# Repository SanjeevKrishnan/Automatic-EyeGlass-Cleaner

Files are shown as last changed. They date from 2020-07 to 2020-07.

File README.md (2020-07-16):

# Automatic EyeGlass Cleaner
Inter IIT Tech Meet 2019

## Abstract

Aim of this project is to make a self-automated Eyeglass Cleaner that can cleanse and dry any spectacles.

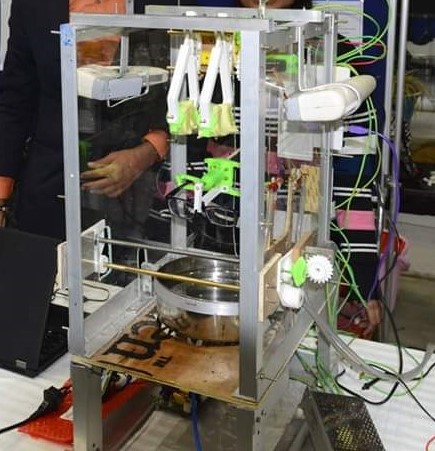
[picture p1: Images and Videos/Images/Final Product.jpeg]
Final Product


## Motivation

<p align="justify">In this fast and busy world, we fail to take care of our own minute personal cleanliness. But when we enter the professional world, all these small things get noticed. And also, these small things pile up to big issues which in turn affects us directly. In this, our spectacles take a major part because eyes are our index. An easily operable machine which can clean our spectacles during our coffee time will be of high use, especially in professional and public spaces.<br><br>Eyeglasses cleaners available presently in the market are costly but are not versatile. They either do ultrasonic cleaning or splashing water and drying. But still, it leaves smudges on the lenses. And also they might take much time for this simple task and majorly nowhere automatic wiping is available. This process is clumsy and can be automated which would give the user complete hands-free experience.<br><br>So we planned on designing a machine that can clean, rinse, dry, and wipe the eye-glass in less time.</p>

## Components

* 2x Air Blower
* Capacitors
* 2x Cytron Motor Drive
* 1x DC 900 rpm motor
* 2x DC 300 rpm motor
* 2x DC Solenoid Valve
* Fuse
* Inductors
* 1x 12V DC Power Adapter
* Relay
* 4x 5V Relay Module
* Resistors
* 1x Rotary Encoder
* 1x Servo Motor
* Transformers
* Transistors
* Ultrasonic Transducer
* 1x Water Pump

## Workflow

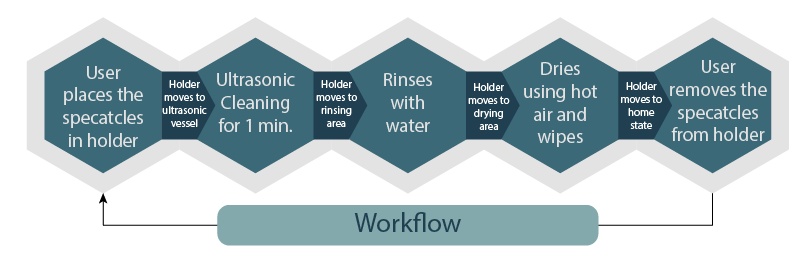
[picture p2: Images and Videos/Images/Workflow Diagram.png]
Worflow Diagram


## Mechanical Aspect of the Design

### Structure

<p align="justify">It is a cuboidal frame structure made up of aluminum channel covered with transparent acrylic sheets to allow users to see the whole cleaning process. Wiper and hot air blower are placed at the top, water rinser is placed at the middle, and ultrasonic cleaning vessel is placed at the bottom. Water storage is placed above the structure, ultrasonic circuit, and water pump is placed in a separate chamber below ultrasonic vessel separated by plywood and all other electronic components are placed at the backside of the structure separated from the structure by acrylic sheet to protect components from water.</p>

### Holder

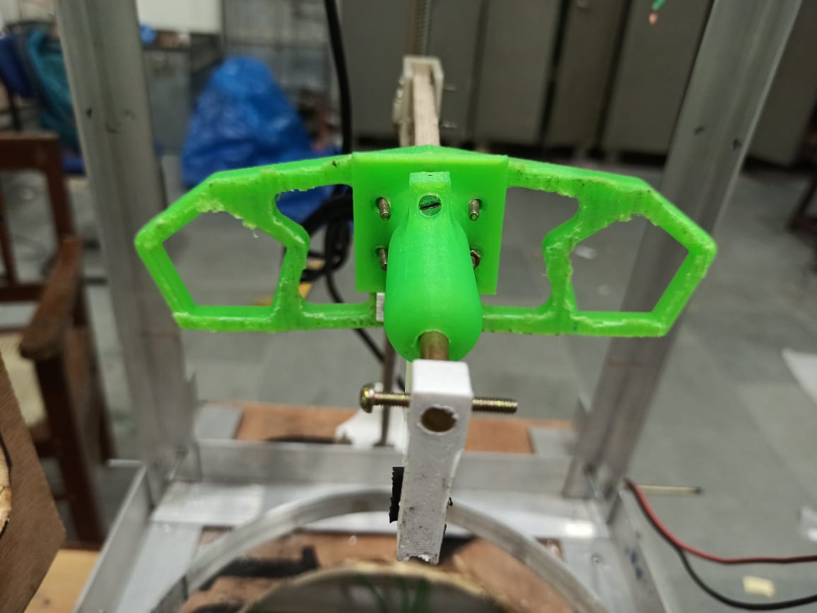
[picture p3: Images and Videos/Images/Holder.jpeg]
Holder


We have designed a special holder for mounting the eyeglasses. Eyeglasses comes in different shapes and sizes. So we have made a holder that can adjust itself to hold all types of eyeglasses.

### Ultrasonic Cleaning

<p align="justify">There is a vessel at the bottom which is connected with an ultrasonic transducer which produces ultrasonic waves in the liquid filled inside the vessel by changing electrical signals to mechanical waves. The waves create cavitation in the liquid. These cavitations collapse with enormous energy due to which high temperature and pressure are generated and thus help in cleaning the glasses.</p>

### Rinsing

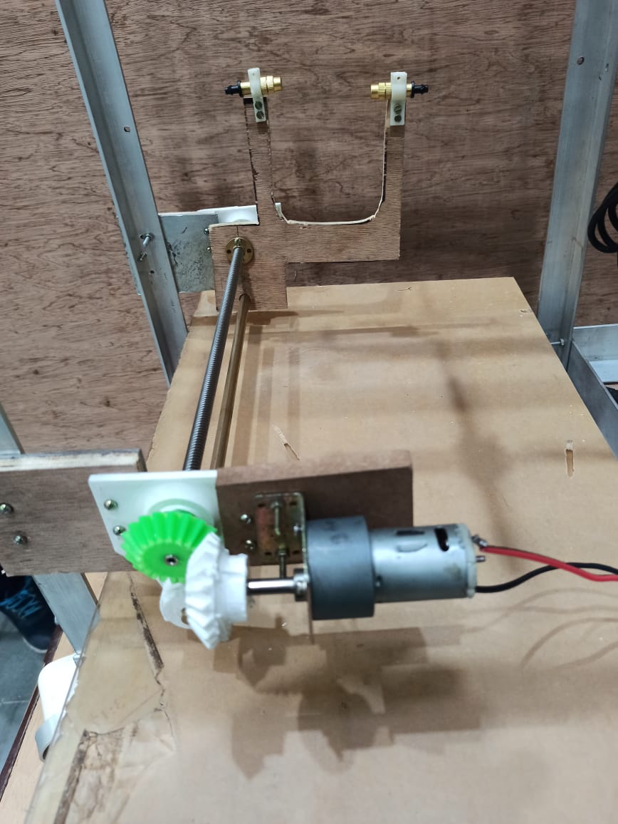
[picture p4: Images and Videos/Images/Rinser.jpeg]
Rinser


<p align="justify">After ultrasonic cleaning, eye-glass is lifted to the middle of the machine where it is rinsed with water with the help of a ‘U’ shaped structure with two nozzles placed in front and back of the lenses. This rinser runs perpendicular to the eyeglass splashing water on the eyeglasses.</p> 

### Drying and Wiping

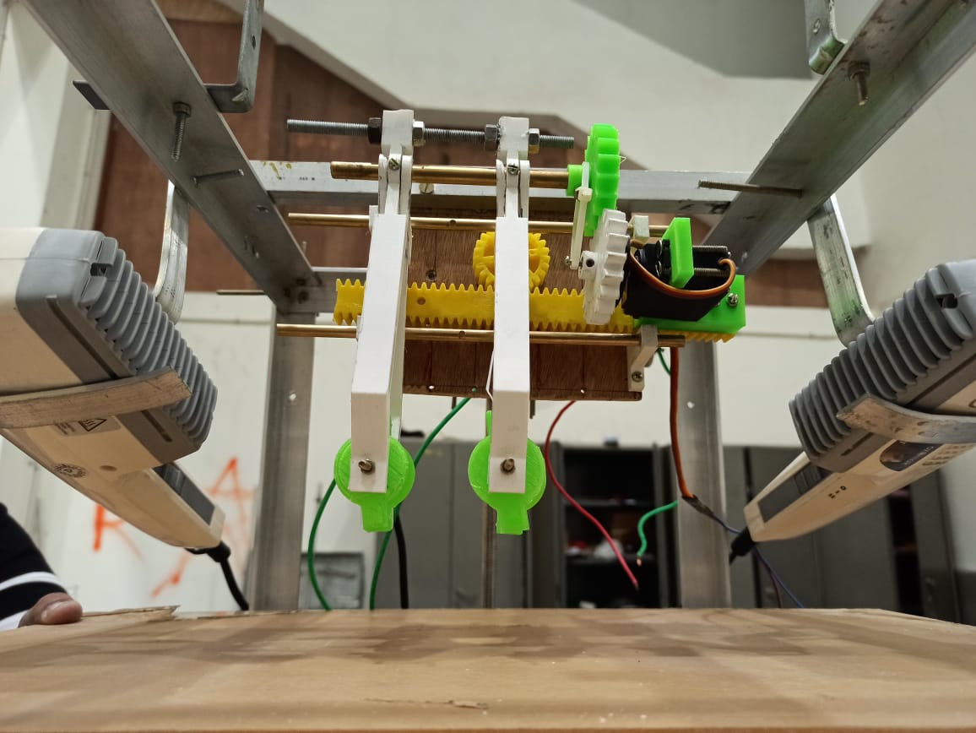
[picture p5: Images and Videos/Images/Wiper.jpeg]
Wiper


<p align="justify">After rinsing, eyeglasses move to the last level, to the top of the machine, where it is dried and wiped. There are hot air blowers on the two side walls of the machine which blows hot air on the spectacle which helps in removing wetness from the frame. Then it is wiped with a sponge wrapped with a microfiber cloth. There are 4 circular disks with this kind of wiping material covering both sides of both the lenses. This wiper works on the rack and pinion mechanism.</p>

### Traversal

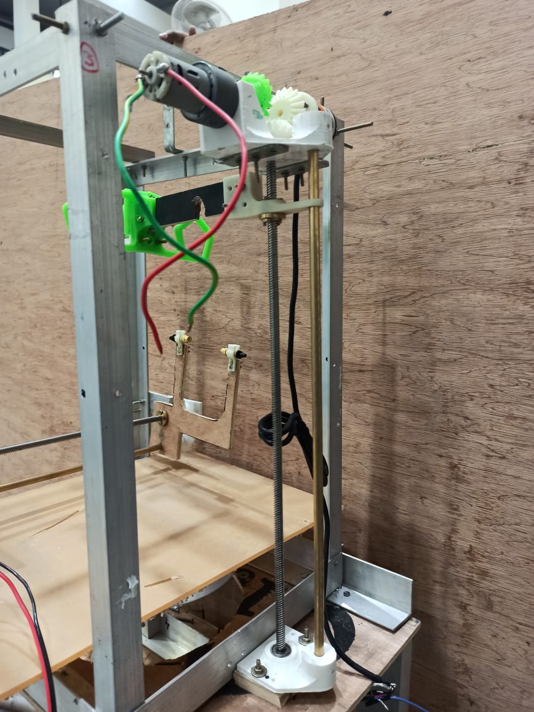
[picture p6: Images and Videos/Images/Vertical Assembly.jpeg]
Vertical Assembly


<p align="justify">The eyeglass holder is connected to a vertical lead screw which helps the eye-glass to move to different levels for different processes. This vertical lead screw is operated by a 900 rpm DC motor which is placed perpendicular to the lead screw and both are coupled with a pair of bevel gear. Its feedback is taken with the help of a rotary encoder which is again placed in the same fashion as the motor.</p>

## Electronics Aspect of the Design

### Microcontroller

Arduino Mega 2560 R3 is used as the microcontroller board.

### Sensors

* Rotary Encoder is used to get the coordinate feedback of vertical assembly(holder).
* Hall Sensor is used to sense the home state(start position) of vertical assembly.

### Actuators

* Johnson 900 rpm DC motor is used for traversal of the holder.
* Johnson 300 rpm DC motors are used for traversal of the rinser and movement of wiper.
* Servo Motor is used for wiping action.

### Other Controllers

* Cytron Motor driver is used to control DC motors
* 5V Relay module is used to switch on/off the ultrasonic cleaner, water pump, and air blowers.

### Other Components

* DC 12V 80W water pump is used to spray water during rinsing action.
* 12V Solenoid Valves are used to control water movement between the tank and ultrasonic vessel

### Power

* Ultrasonic Cleaner circuit and air blowers are directly powered from 220V AC supply.
* 12V DC Power Adapter is used to convert 220V AC to 12V DC to power solenoid valves, water pump, and motor drivers.
* IC LM7809, IC LM7806, IC LM7805 are used to convert 12v DC to 9V DC, 6V DC, 5V DC respectively to power Arduino, servo motor, encoder, relay module.

## Cost Structure

| **Components** |**Cost(INR.)**|
|---|---|
| Air Blower | 1300 |
| Aluminium Channels and Rods | 800 |
| Arduino Mega | 800 |
| Capacitors | 300 |
| Cytron Motor Driver | 3000 |
| DC Motors | 1050 |
| DC Solenoid Valve | 250 |
| Fuse | 35 |
| Hose, Pipes, and Brass connectors | 450 |
| Inductors | 150 |
| Power Adapter | 1500 |
| Relay | 100 |
| Relay Module | 450 |
| Resistors | 900 |
| Rotary Encoder | 1500 |
| Servo Motor | 150 |
| Transformer | 230 |
| Transistors | 100 |
| Ultrasonic Transducer | 800 |
| Water Pump | 700 |
| Miscellaneous | 235 |
| **Total** | **14000**  |

## Applications

* Optical showrooms-To clean customers’ spectacles
* Eye clinics - To clean patients’ spectacles
* Theatres - To clean 3D glasses 
* Offices - Workers can clean their spectacles
* Shopping Malls - People can spend their wait time in cleaning their spectacles

## Limitations

* Time taken per eyeglass is bit high.
* Ultrasonic cleaning circuit has to be switched on manually.

## Future Improvements

* Actuations can be made fast to reduce cleaning duration.
* Indications and Error messages can be displayed using an LCD display module.
* Ultrasonic Cleaning process can also be automated.

## Team Members

1. [Panuganti Shiva Sri Teja Kumar](https://github.com/shivasriteja)
2. [Rishika Chandra](https://github.com/chandrarishika14)
3. [Sanjeev Krishnan R.](https://github.com/SanjeevKrishnan)
4. [Suja G.](https://github.com/suja-g)
5. [Ujjwal Baranwal](https://github.com/ujjwal-baranwal)
6. [Yashutosh Bansal](https://github.com/yashutoshbansal)
7. [Yawan Gupta](https://github.com/yawangupta)

## Mentors

1. [Anant Shandilya](https://github.com/Anant-Shandilya)
2. [Shubhanshu Agarwal](https://github.com/Shubhanshu07)

## References

<https://techblog.ctgclean.com/2012/01/ultrasonics-transducers-resonance/>

<https://www.americanpiezo.com/standard-products/ultrasonic-power-transducers.html>

<https://www.allaboutvision.com/en-in/eyeglasses/faq/eyeglass-frame-size/>

<https://www.svce.ac.in/departments/physics/ph16151/UNIT%204%20Ultrasonics%20.new.pdf>

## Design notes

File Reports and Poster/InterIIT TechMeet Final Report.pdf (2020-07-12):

# Engineer’s Conclave

Low-Prep Event (150 Points)

# Project Report

## Project Name: Automatic Eyeglass Cleaner

## Institute Name: Indian Institute of Technology Roorkee

## Team:

Serial No. | Team Member Name | Enrollment No.
1. Panuganti Shiva Sri Teja | Kumar | 18113091
2. | Rishika Chandra | 18115084
3. | Sanjeev Krishnan R. | 18110021
4. | Suja G. | 18122025
5. | Yawan Gupta | 17118080

## Problem addressed:

Eyeglasses cleaners available presently in the market are costly but are not versatile. They either do ultrasonic cleaning or splashing water and drying. But still, it leaves smudges on the lenses. And also they might take much time for this simple task and majorly nowhere automatic wiping is available. This process is clumsy and can be automated which would give the user complete hands-free experience.

So we planned on designing a machine that can clean, rinse, dry and wipe the eye-glass in less time.

## Proposed Solution:

We have designed and manufactured a machine which cleans the eyeglasses automatically by combining four processes-
1. Ultrasonic cleaning
2. Rinsing
3. Drying
4. Wiping

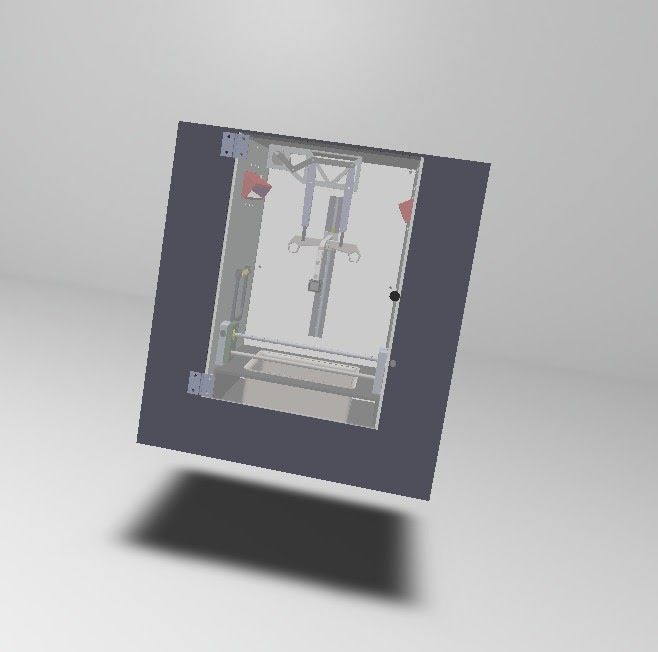
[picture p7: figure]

It cleans the eyeglass with ultrasonic waves which helps it to clean the nook and corner. Then it is rinsed with water by splashing water jet on lenses which helps in removing smudges and fingerprints. Then it is dried by blowing mild hot air to remove wetness on the frame and then wiped with specially designed wiping material wrapped with a microfiber cloth which gives crystal clear appearance to the glasses.

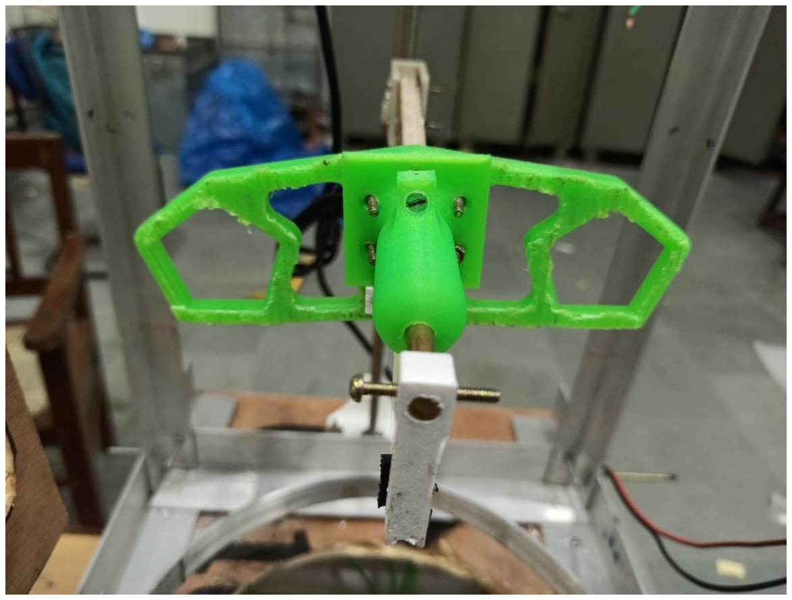
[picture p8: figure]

Mounting the Eye-Glasses

We have designed a special holder for mounting the eyeglasses. Eyeglasses comes in different shapes and sizes. So we have made a holder that can adjust itself to hold all types of eyeglasses.

Movement of Eyeglasses to different levels

The eyeglass holder is connected to a vertical lead screw which helps the eye-glass to move to different levels for different processes. This vertical lead screw is operated by a 900 rpm DC motor which is placed perpendicular to the lead screw and both are coupled with a pair of bevel gear. Its feedback is taken with the help of a rotary encoder which again placed in the same fashion as the motor.

Ultrasonic Cleaning

There is a vessel at the bottom which is connected with an ultrasonic

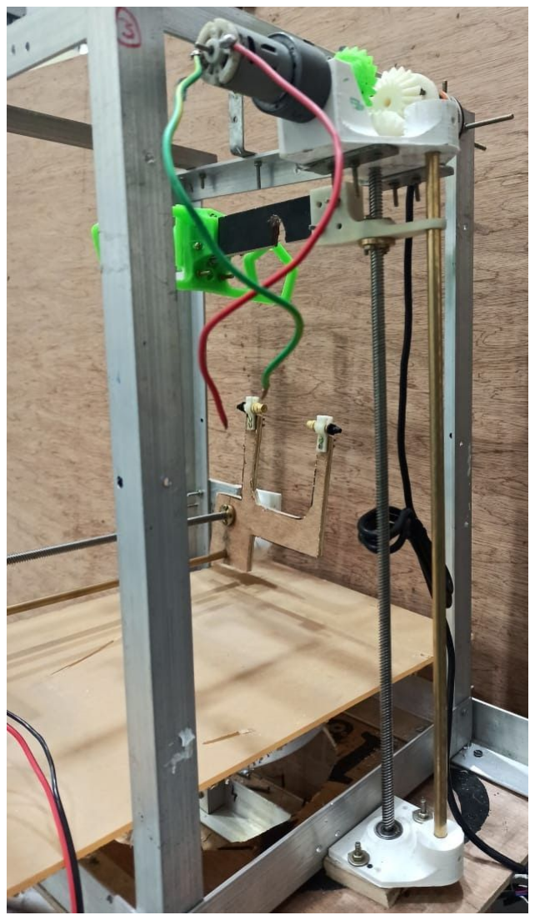
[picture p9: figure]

transducer which produces ultrasonic waves in the liquid filled inside the vessel by changing electrical signals to mechanical waves. The waves create cavitation in the liquid. These cavitations collapse with enormous energy due to which high temperature and pressure are generated and thus help in cleaning the glasses.

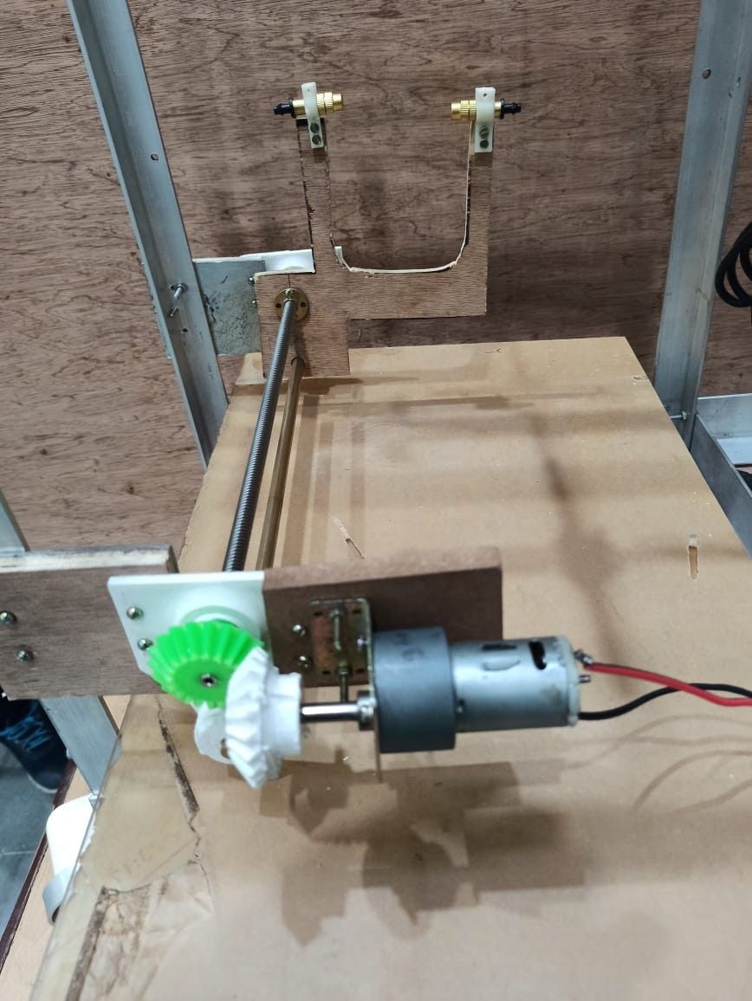
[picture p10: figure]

Rinsing

After ultrasonic cleaning, eye-glass is lifted to the middle of the machine where it is rinsed with water with the help of a ‘U’ shaped structure with two nozzles placed in front and back of the lenses. This rinser runs perpendicular to the eyeglass splashing water on the eyeglasses.

Drying and Wiping

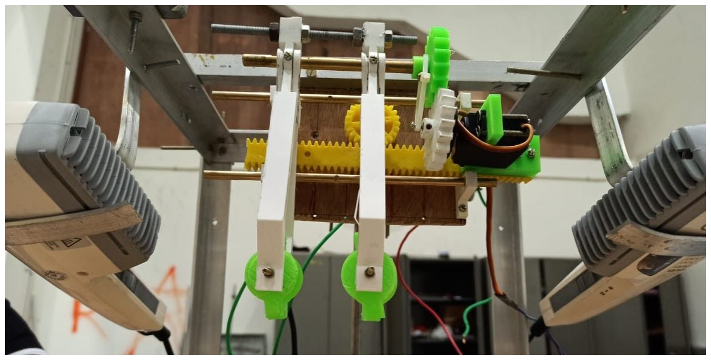
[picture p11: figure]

After rinsing, eyeglasses move to the last level, to the top of the machine, where it is dried and wiped. There are hot air blowers on the two side walls of the machine which blows hot air on the spectacle which helps in removing wetness from the frame. Then it is wiped with a sponge wrapped with a microfiber cloth. There are 4 circular disks with this
kind of wiping material covering both sides of both the
lenses. This wiper works on the rack and pinion mechanism.

After wiping is done holder is again brought back down from where it is taken out by the user.

## Summary:

## - Test Results:

We tried wiping with wiper working on a double scotch yoke mechanism in which one actuator is used to do two motions in the perpendicular direction(moving wiper parallel and the open wiper). It was not much efficient. The required force was not acquired. So we changed it to rack and pinion mechanism in which we use one actuator for sliding the wiper along spectacles and one servo motor for sweep action of the wiper.
We tried drying the spectacle with two normal hair dryers. It was taking more time than expected. So we have attached one more blower on the top.
We tried ultrasonic cleaning with one transducer to transmit ultrasonic waves. Each transducer has some range of area coverable. Expectations were not met as our area of the vessel was more than that of the allowed range of the transducer. So we added one more transducer. Now the whole surface is covered and expectations are met.

## - Surveys:

We made surveys on the sizes of lenses. The average range of temple length came out to be 120mm to 150mm. The average bridge length ranges from 14mm to 24mm and the width of lenses ranges from 40mm to 62mm.

We made a survey to find approximately how much time one person would wish to spend to clean his eye-glass. Results came out to be 1-2 mins.

## - References:

- https://techblog.ctgclean.com/2012/01/ultrasonics-transducers-resonance/
- https://www.americanpiezo.com/standard-products/ultrasonic-power-transducer s.html (https://www.americanpiezo.com/standard-products/ultrasonic-power-transducers.html)
- https://www.allaboutvision.com/en-in/eyeglasses/faq/eyeglass-frame-size/
- https://www.svce.ac.in/departments/physics/ph16151/UNIT%204%20Ultrasoni cs%20.new.pdf (https://www.svce.ac.in/departments/physics/ph16151/UNIT%204%20Ultrasonics%20.new.pdf)

## - Video Links

*
:

(* = Optional)

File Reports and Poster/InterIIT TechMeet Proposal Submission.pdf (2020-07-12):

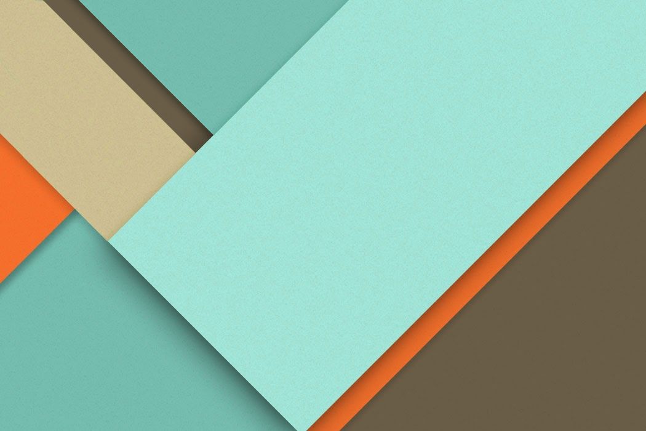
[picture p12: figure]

# Automatic Eye-Glass Cleaner

─

## Models And Robotics Section

### Indian Institute of Technology Roorkee

# Contents

─

Overview | 2
Project Motivation | 2
Other Products available in the market and their disadvantages | 2
Ultrasonic Cleaners | 2
Microfiber Handle Brush Tool | 2
OpticWash Machine | 3
Our solution | 3
Holding and Movement | 3
Cleaning | 4
Rinsing | 4
Drying | 4
Wiping | 5
Cost Structure | 5
Market Analysis | 6
Target Market | 6

## Overview

We have designed an automatic Eye-Glass cleaner which cleans the spectacles with ultrasonic cleaning technology, rinses with water and then dries it by blowing and wiping.

## Project Motivation


In this fast and busy world, we fail to take care of our own minute personal cleanliness. But when we enter the professional world, all these small things get noticed. And also, these small things pile up to big issues which in turn affects us directly. In this, our spectacles take a major part because eyes are our index. An easily operable machine which can clean our spectacles during our coffee time will be of high use, especially in professional and public spaces.

## Other Products available in the market and their

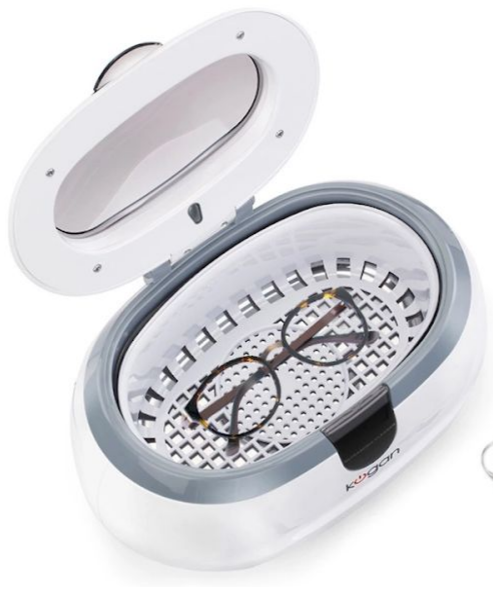
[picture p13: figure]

## disadvantages

## Ultrasonic Cleaners

- These cleaners cannot dry the glasses. So the glasses come out of the machine in a wet state and the person has to wipe it on his own.
- They can’t remove smudges from the glasses.
- These cleaners cannot rinse and wipe the glasses.

## Microfiber Handle Brush Tool

- This tool just cleans the lens. It does not help us with cleaning the frame especially corners.
- It has to be changed once in a while to get the same level of cleanliness.

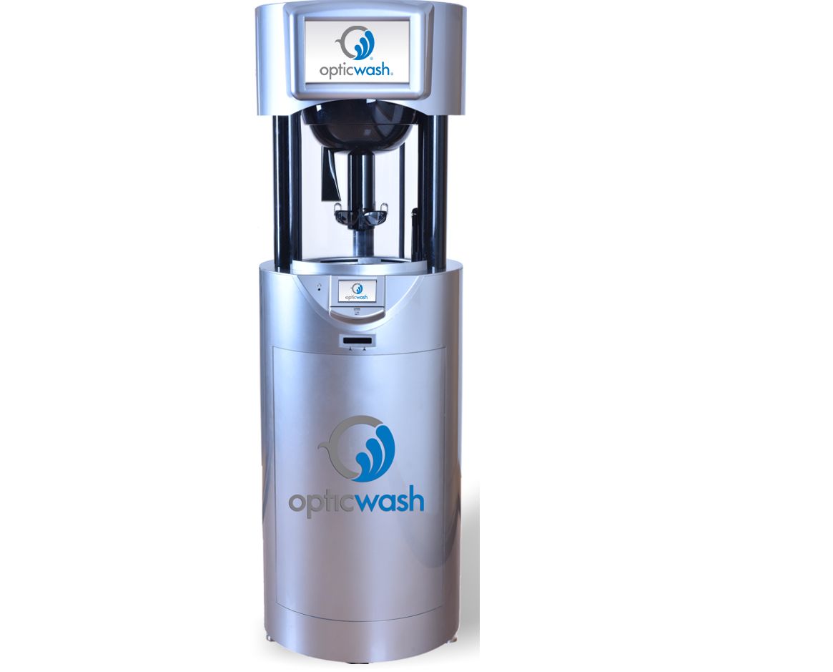
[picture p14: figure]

## OpticWash Machine

- It does not clean nook and corners as it just splashes water on the spectacles.
- Smudges do not get removed very efficiently as it is not wiping the lenses.
So, we have designed a machine which cleans with ultrasonic, rinses with water, dries by blowing air and wipes the glasses with foam so that user can use it directly out from the machine.

## Our solution

## I. Holding and Movement

In our solution, we have designed a unique spectacle holder which is easy for users to place their spectacle and also it is designed to be adjustable so that all kinds of spectacles can be placed in the holder with hassle free operation. This holder holds the spectacle at three points namely middle of bridge and starting edges of left and right temples. This holder is attached to a lead screw for easy and accurate actuation in vertical direction.

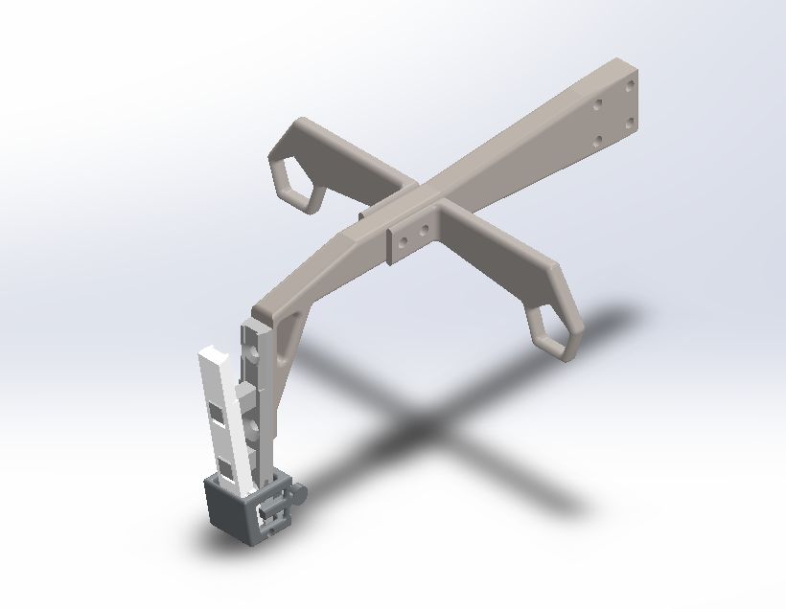
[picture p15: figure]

## II. Cleaning

In an ultrasonic cleaner, the object to be cleaned is placed in a chamber containing a suitable solution. An ultrasound generating transducer built into the chamber produces ultrasonic waves in the fluid by changing size in concert with an electrical signal oscillating at ultrasonic frequency. This creates compression waves in the liquid of the tank which creates cavitation in the liquid. These cavitation collapse with enormous energy, temperatures and pressures in the order of 5,000 K and 135 MPa is achieved. The circuit works if we drive the transducer from a square wave fed through a series LC circuit tuned to the transducer frequency. A piezoelectric ultrasonic transducer’s equivalent circuit is a capacitor in parallel with a series tuned LCR circuit. With just half an H bridge square wave drive, the transistors must charge and discharge that parallel equivalent capacitor on each half-cycle.

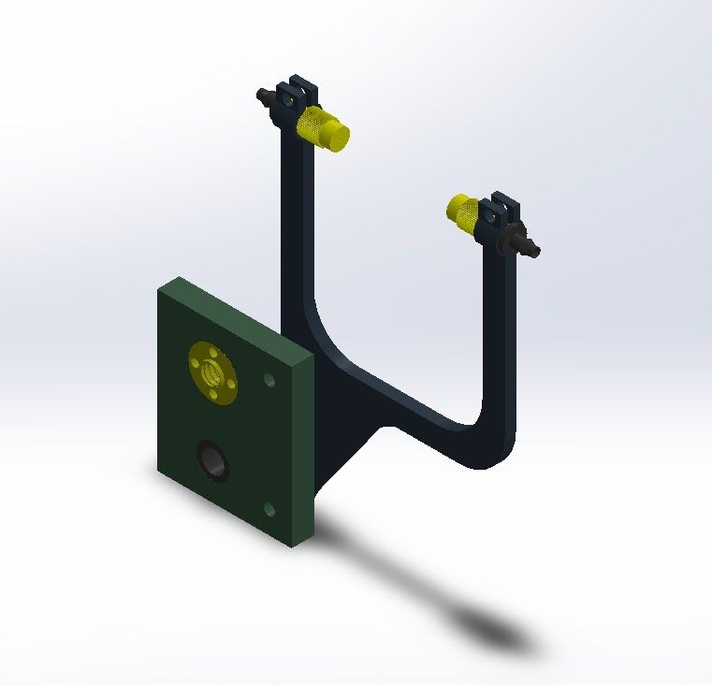
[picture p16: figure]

## III. Rinsing

After cleaning, the glasses have some chemicals solutions which need to be cleaned so we do this process by using a pump which is present in the water container. It pumps the water from container to hoes through pipes.

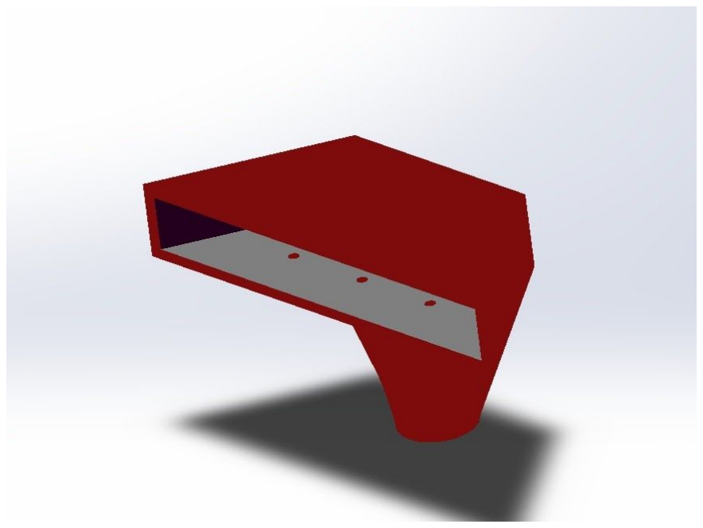
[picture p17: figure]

## IV. Drying

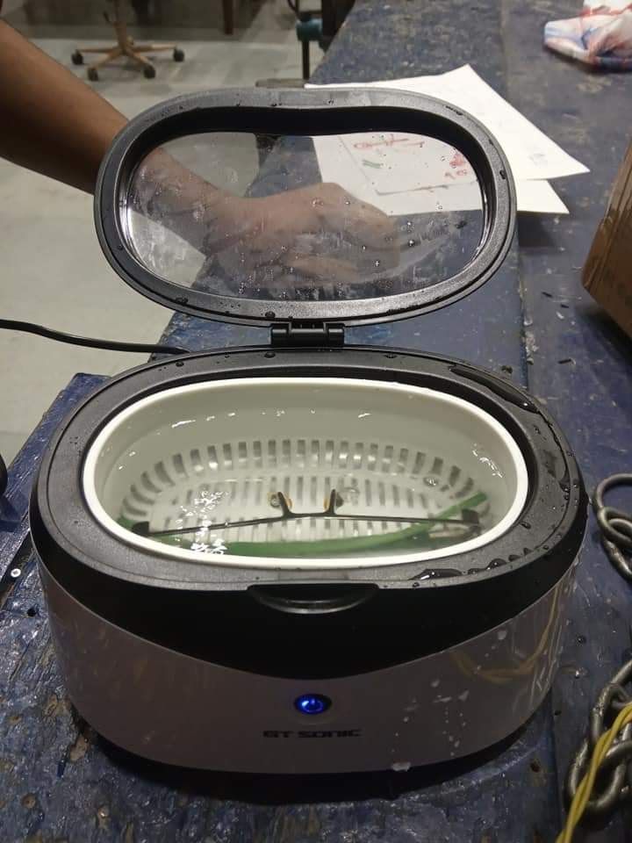
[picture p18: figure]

After rinsing, the next process is drying in which water from the glasses are removed by blowing air. In our machine, this process is carried out by the compressor which blows air through a pipe which is connected to the blower.

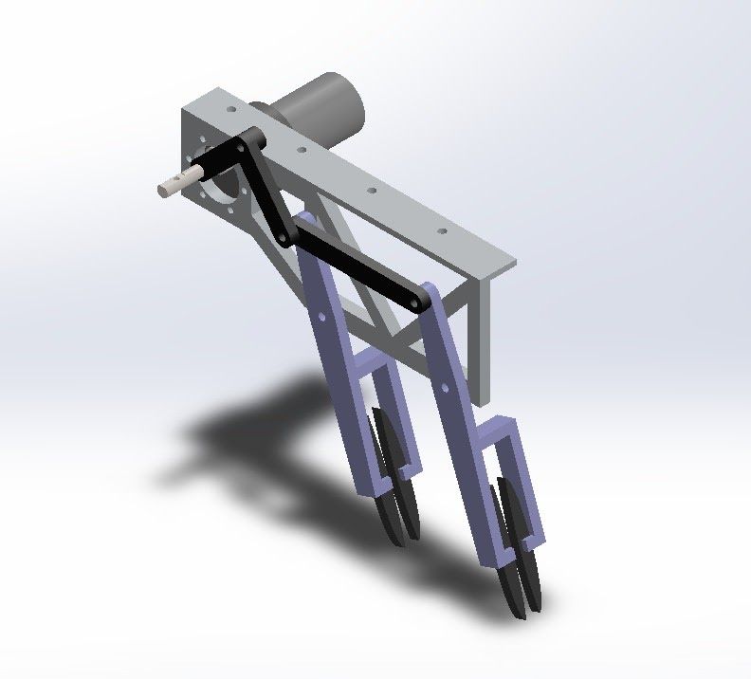
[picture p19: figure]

## V. Wiping

To remove smudges from the glasses, gentle wiping is applied by using foam which circulates on the glasses so that we get a crystal clean finish.

## Cost Structure

Components | Cost
Transformer | Rs. 230
Relay | Rs. 100
Resistors | Rs. 900
Capacitors | Rs. 300
Inductors | Rs. 150
Fuse | Rs. 35
Ultrasonic Transducer | Rs. 800
Transistors | Rs. 100
Servo motors | Rs. 150
DC Motors | Rs. 1050
Cytron Motor Drive | Rs. 3000
Rotary Encoder | Rs. 1500
Water Pump | Rs. 700
DC Solenoid Valve | Rs. 250
Relay Module | Rs.450
Power Adapter | Rs. 1500
Air Blower | Rs. 1300
Aluminium Channels and Rods | Rs. 800
Hose,Pipes and brass connecters | Rs.450
Miscellaneous | Rs. 235
TOTAL | Rs. 14000

## Market Analysis

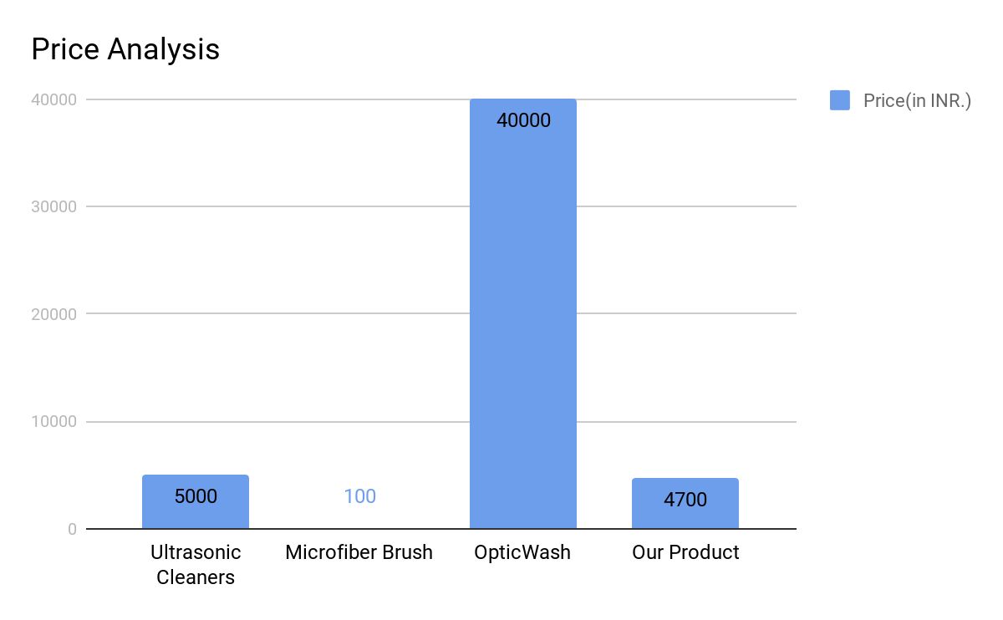
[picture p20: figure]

Ultrasonic cleaner currently available in market can only clean the eyeglass with ultrasonic mechanism which does not involve rinsing with water or drying it. OpticWash machine splashes water on eye glass and dries by blowing air but does not wipe which leave smudges on the lens. Microfiber brush can be used to wipe the lens to remove dust and smudges manually. But our product does all these things- cleaning with ultrasonic cleaner rinsing with water and drying by blowing air and also wiping it with wiper. But still we are able to produce it for around Rs. 5000. This would help our product to take a steady place in the market. Also, Rs.5000 is affordable for most of the corporate offices which is our primary target market.

## Target Market

Our spectacle cleaner can be used at-
- Optical showrooms
- Eye clinics
- Offices
- Shopping Malls
- Theatres

Optical showrooms and eye clinics is obviously a “for-sure” target market because eye-glass cleaning is one of their major jobs but they do it manually. So now we have come up with a really cheap machine which would make their job easier, more professional and of course anything done with machine gives user satisfaction. In offices where they expect you to be neat and tidy to get a professional touch, these machines would be of great use as you can get your eye glasses cleaned very fast maybe during a cup of coffee. It can be coupled with Shoe polishing machine which is already there in the market which would make a nice pair in corporate offices. Not only in the professional world, casual places like shopping mall can also be targeted. Especially in theatres user’s own eye glass can also be cleaned as it gives a good movie experience and also 3d glasses which they use in theatres can also be cleaned. As we can see we have a clear and versatile market scope in which we would get a stable place as our cost is really affordable.

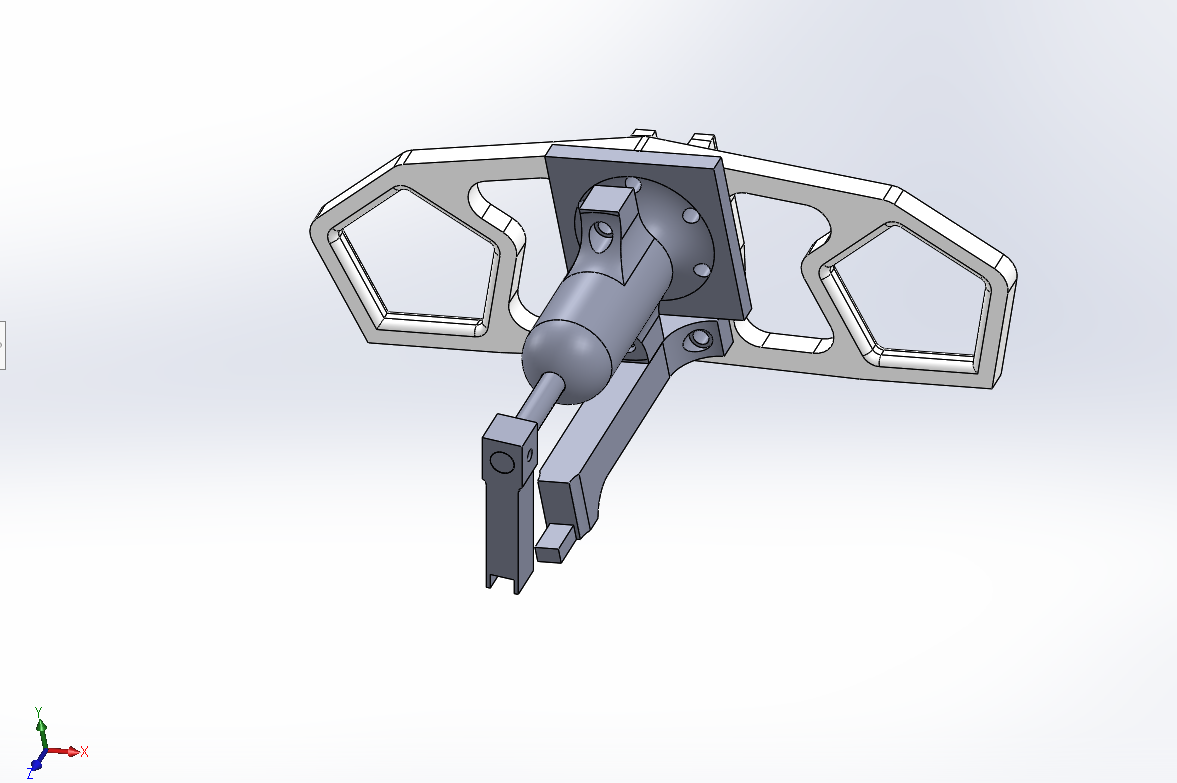
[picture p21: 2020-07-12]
Mechanical Design/Holder/Holder Design.png

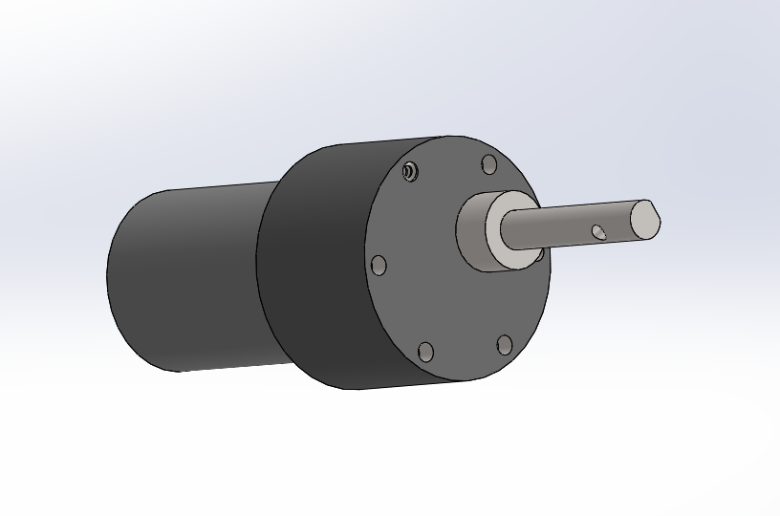
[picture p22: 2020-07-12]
Mechanical Design/Extras/DC motor.png

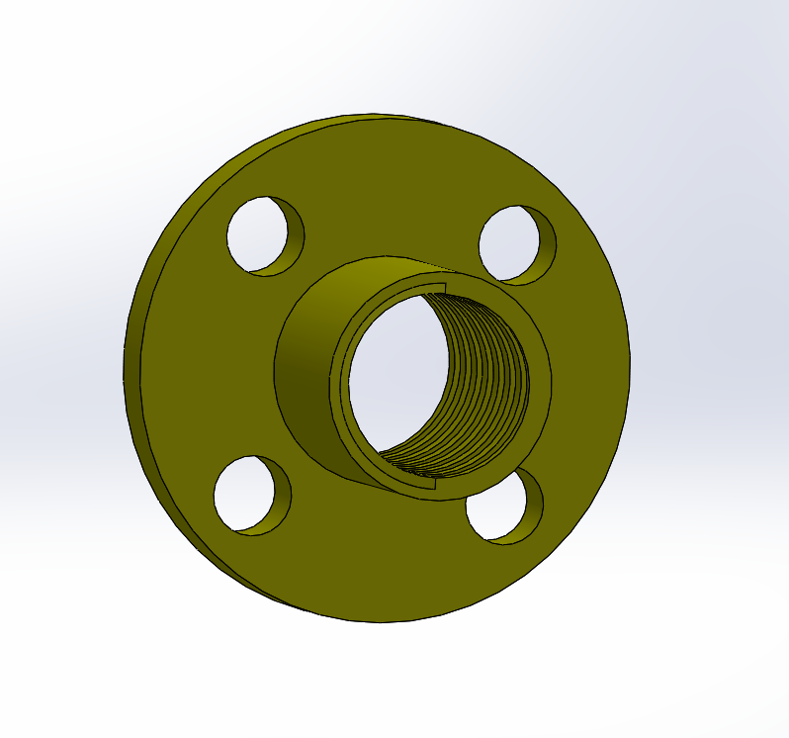
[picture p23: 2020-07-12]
Mechanical Design/Extras/8mm Slider.png

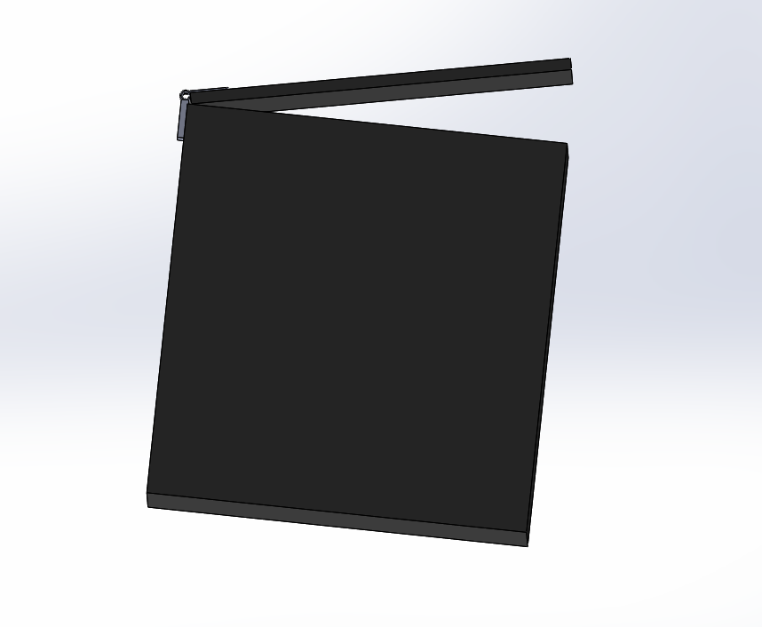
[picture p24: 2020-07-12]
Mechanical Design/Pump/Pump Box Design.png

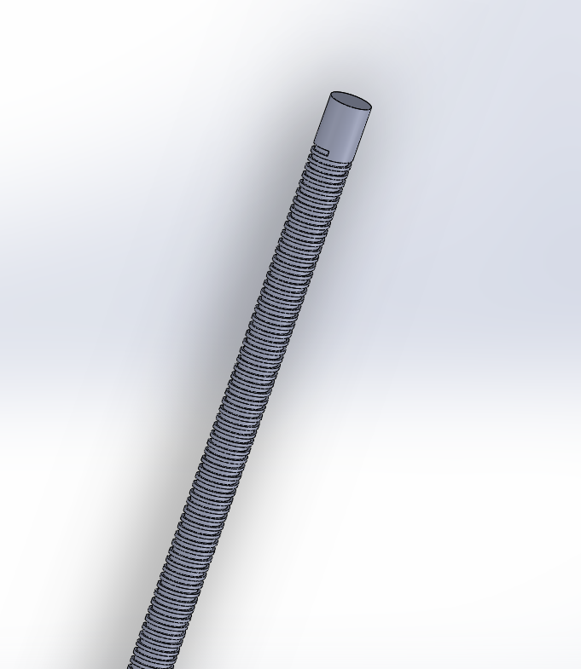
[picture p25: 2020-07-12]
Mechanical Design/Extras/Lead screw.png

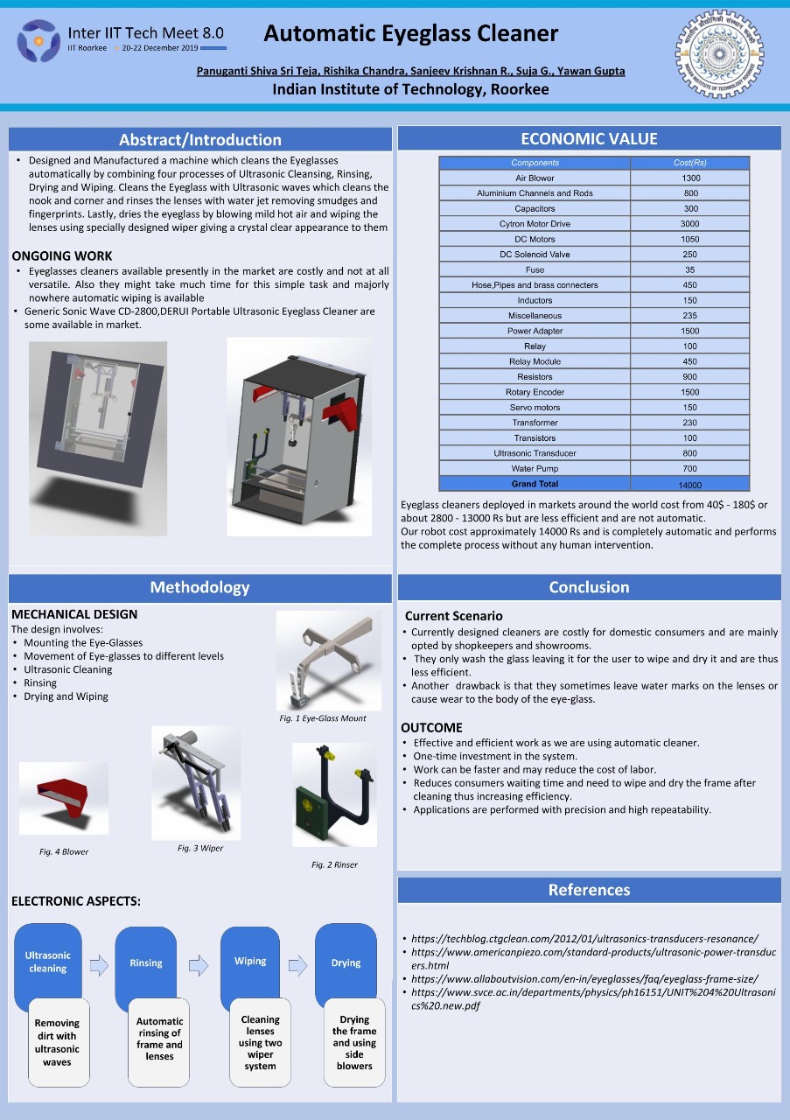
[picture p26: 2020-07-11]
Reports and Poster/InterIIT TechMeet Poster.jpeg

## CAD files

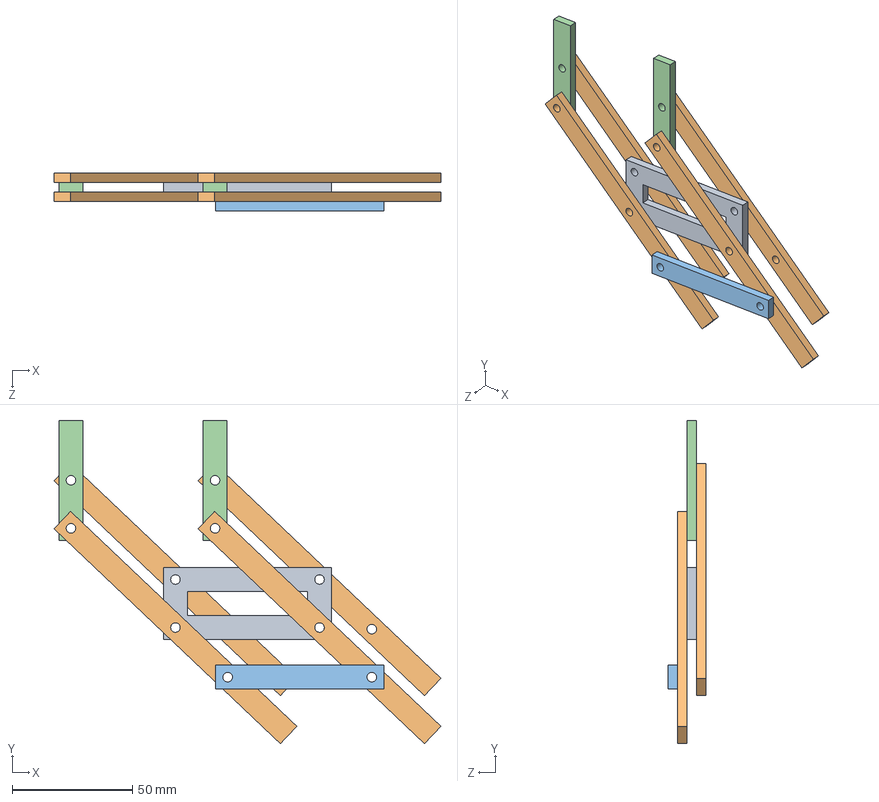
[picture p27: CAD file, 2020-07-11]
Mechanical Design/Wiper/wiper assembly.SLDASM
161.2 x 134.7 x 16.0 mm
Part1^Assem1
Part5^Assem1 x 4
Part6^Assem1
Part7^Assem1 x 2

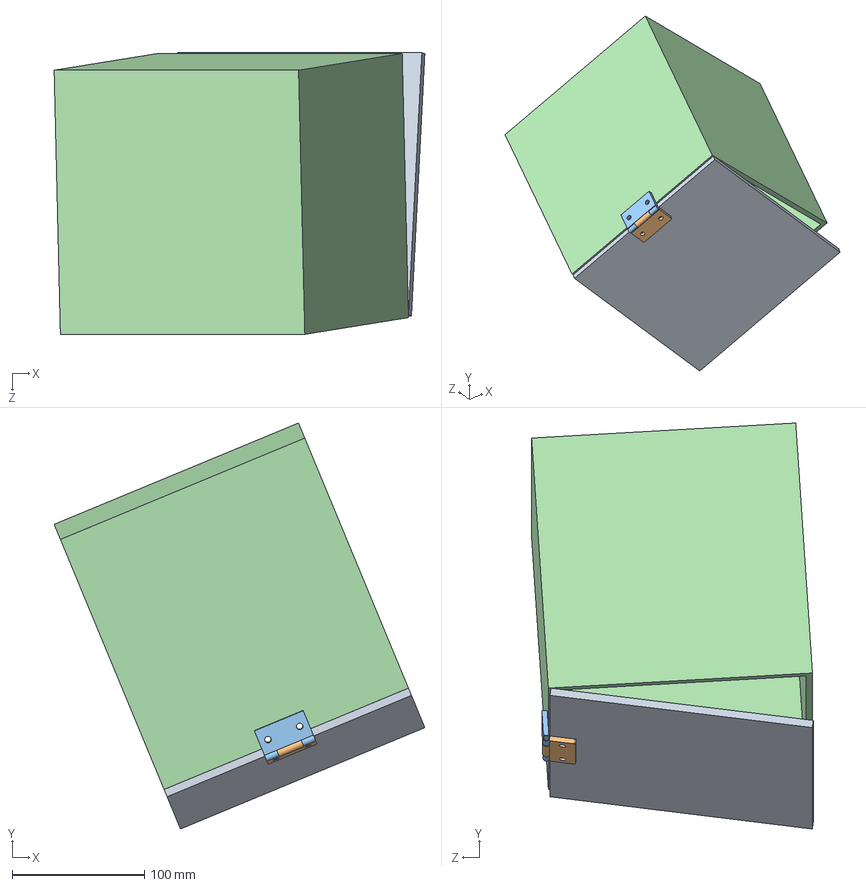
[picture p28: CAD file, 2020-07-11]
Mechanical Design/Pump/pump box.SLDASM
280.2 x 306.9 x 212.9 mm
box lid
hinge1
hinge2
pump

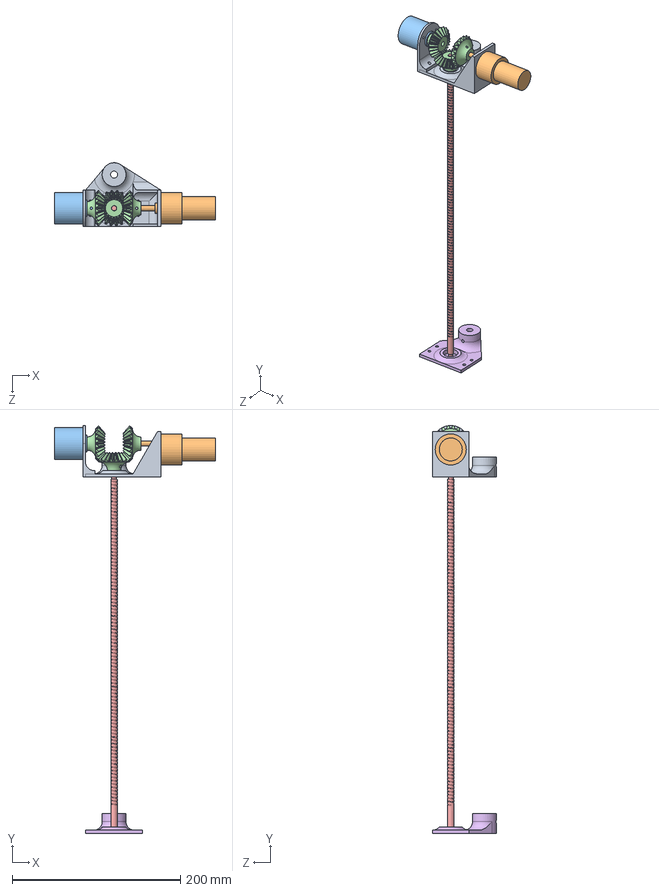
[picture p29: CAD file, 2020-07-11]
Mechanical Design/Vertical Assembly/Final VM assembly.SLDASM
191.7 x 485.5 x 75.7 mm
Motor Mount
DC motor
Encoder
Bevel gear x 3
lead screw VM
lead screw bearing block

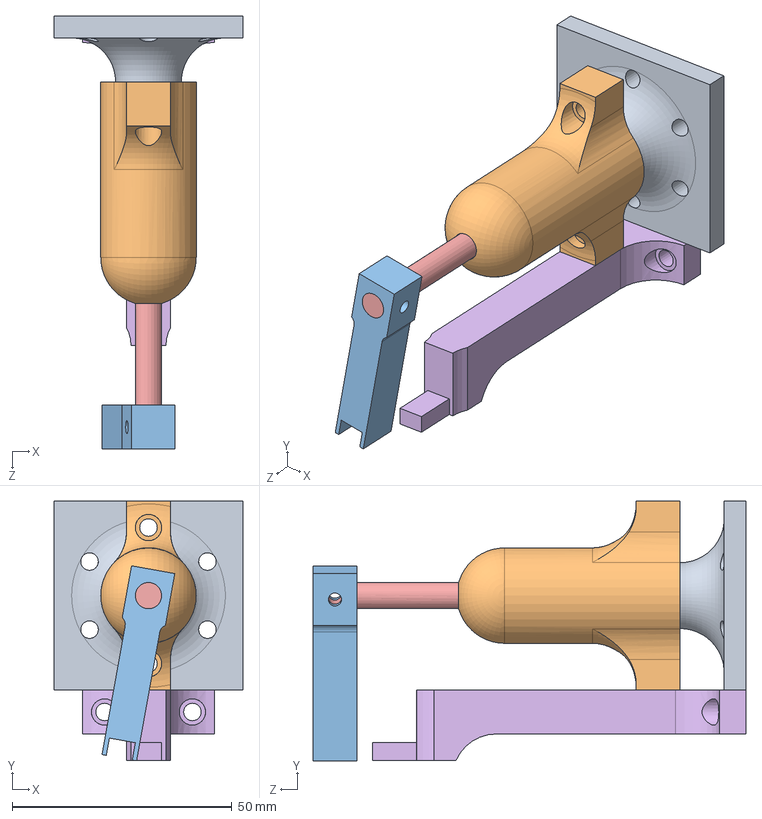
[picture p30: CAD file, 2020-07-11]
Mechanical Design/Holder/Holder assembly.SLDASM
43.0 x 59.1 x 98.6 mm
Base Lock
Lock Cover
Moving Arm
Sliding key
Rod
Base Arm

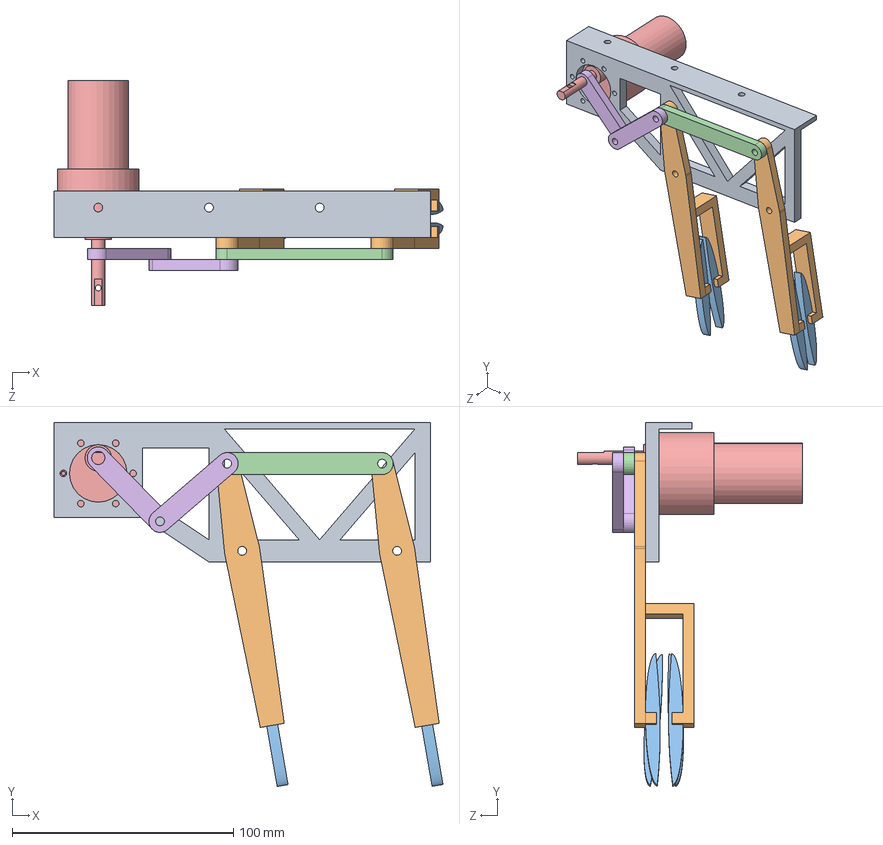
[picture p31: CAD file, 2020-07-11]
Mechanical Design/Wiper/Wiper.SLDASM
175.7 x 164.5 x 101.8 mm
Wiper_Stand
Wiper_Arm-2 x 2
Wiper Blade x 4
Part8^Wiper
DC motor
Part9^Wiper x 2

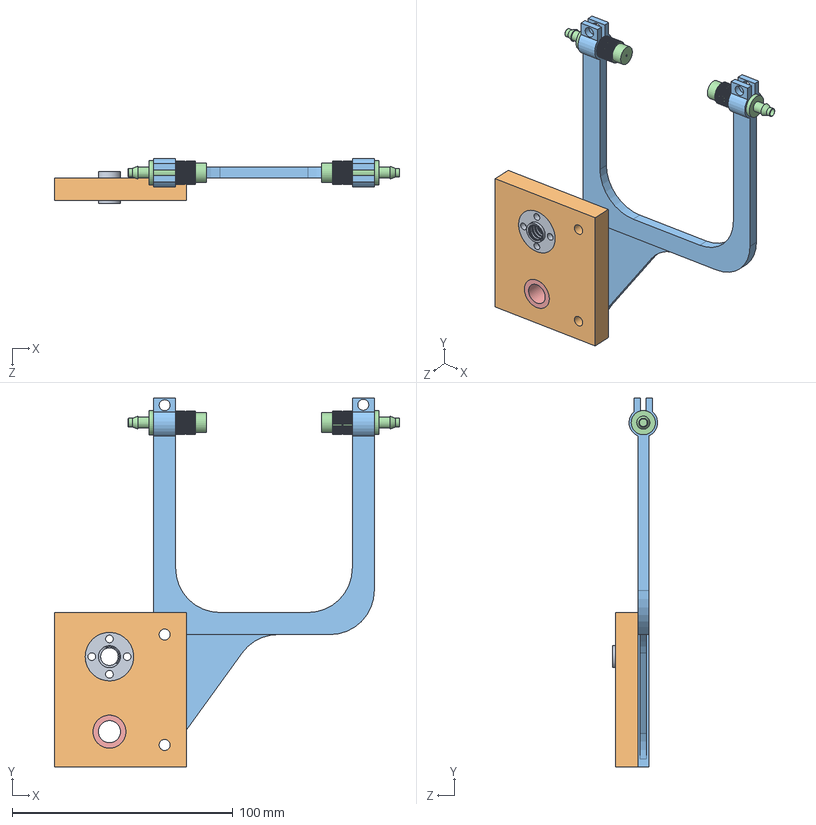
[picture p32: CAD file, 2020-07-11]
Mechanical Design/Rinser/Rinser.SLDASM
156.5 x 167.2 x 20.5 mm
8mm slider
bearing block
nozzle holder
nozzle x 2
linear slider

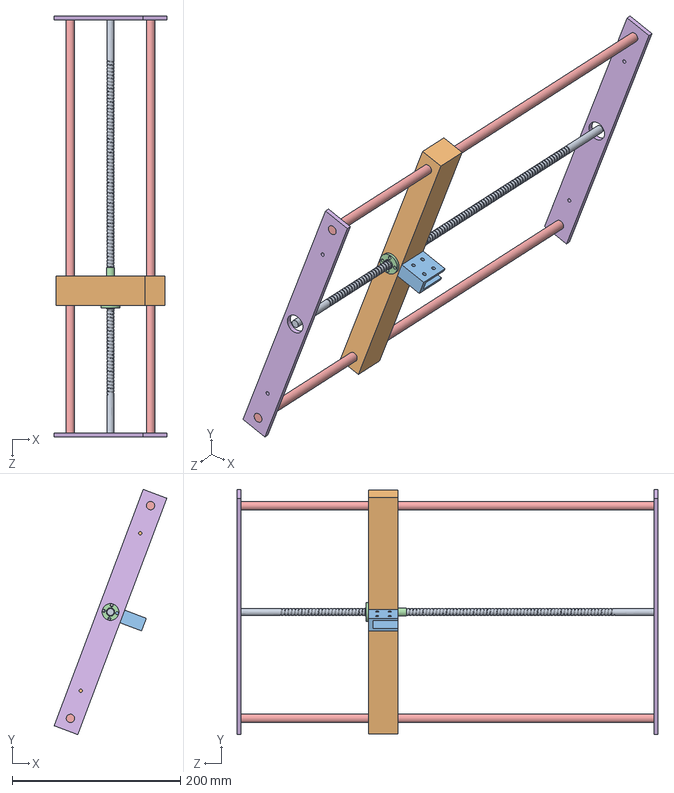
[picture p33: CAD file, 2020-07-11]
Mechanical Design/Vertical Assembly/Vertical Motion Assembly.SLDASM
133.8 x 291.3 x 500.0 mm
lead screw VM
nut mount
gripper mount
8mm slider x 2
VM rods x 2
lead mount x 2

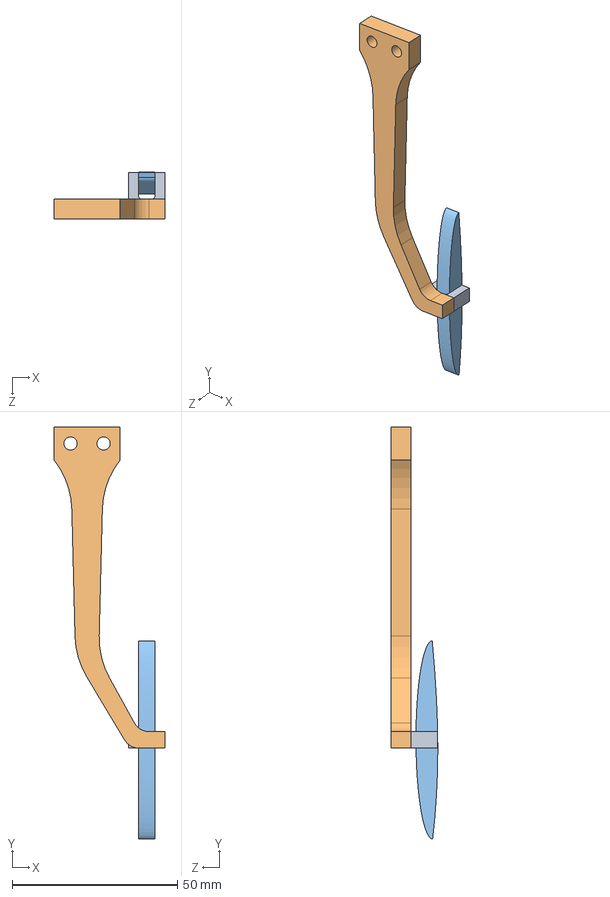
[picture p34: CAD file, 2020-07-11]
Mechanical Design/Wiper/Left Wiper.SLDASM
33.6 x 124.7 x 14.1 mm
Hinge
WiperArm
Wiper Blade

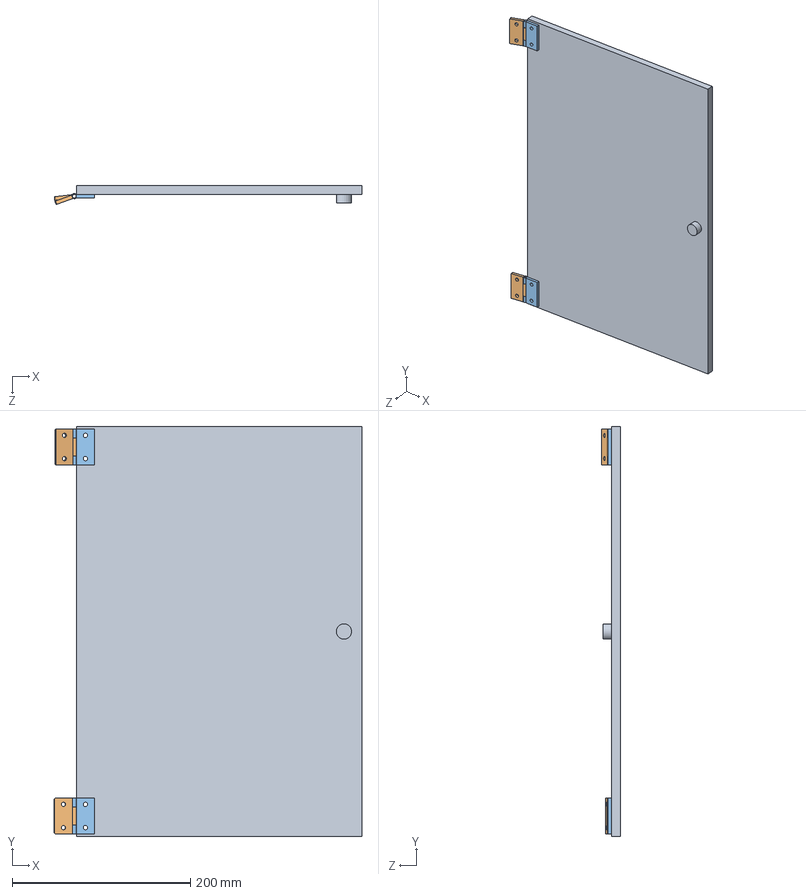
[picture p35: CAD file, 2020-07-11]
Mechanical Design/Inner box/Door.SLDASM
345.1 x 460.0 x 21.5 mm
glass
hinge1 x 2
hinge2 x 2

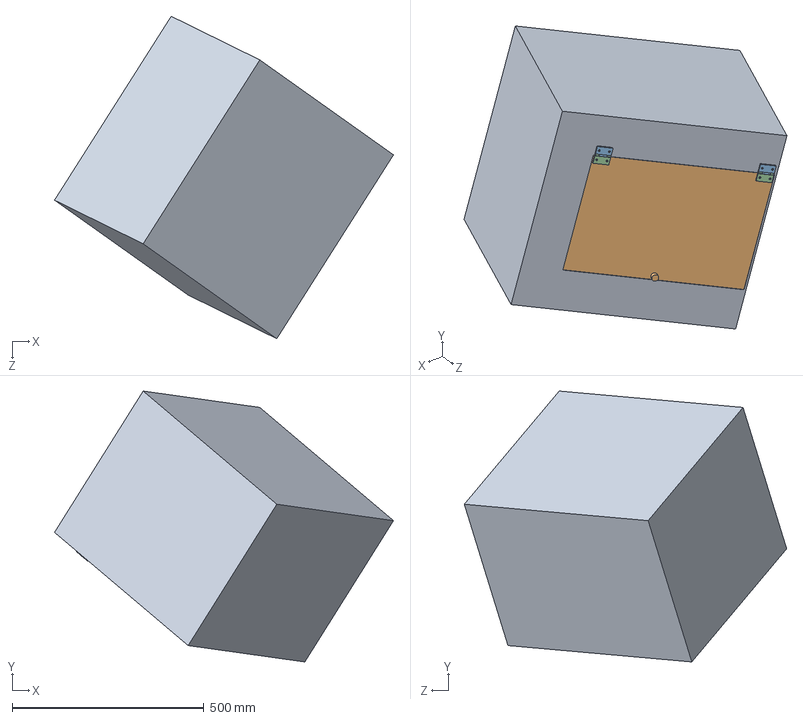
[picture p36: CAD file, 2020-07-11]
Mechanical Design/Inner box/Outer box assembly.SLDASM
884.8 x 707.0 x 841.6 mm
outer box
glass
hinge1 x 2
hinge2 x 2

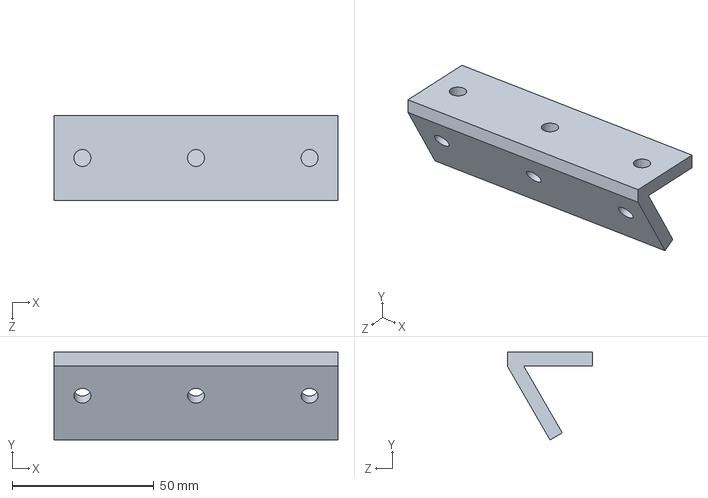
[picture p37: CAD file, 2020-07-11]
Mechanical Design/Blower/blower mount.SLDPRT
100.0 x 31.0 x 30.0 mm

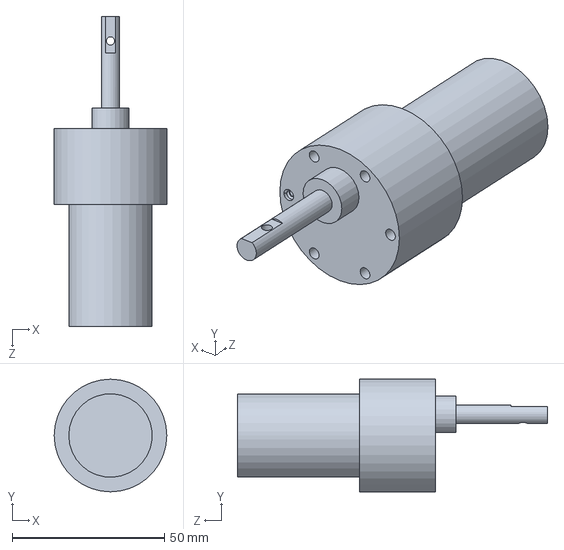
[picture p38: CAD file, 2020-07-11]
Mechanical Design/Extras/DC motor.SLDPRT
37.0 x 37.0 x 101.8 mm

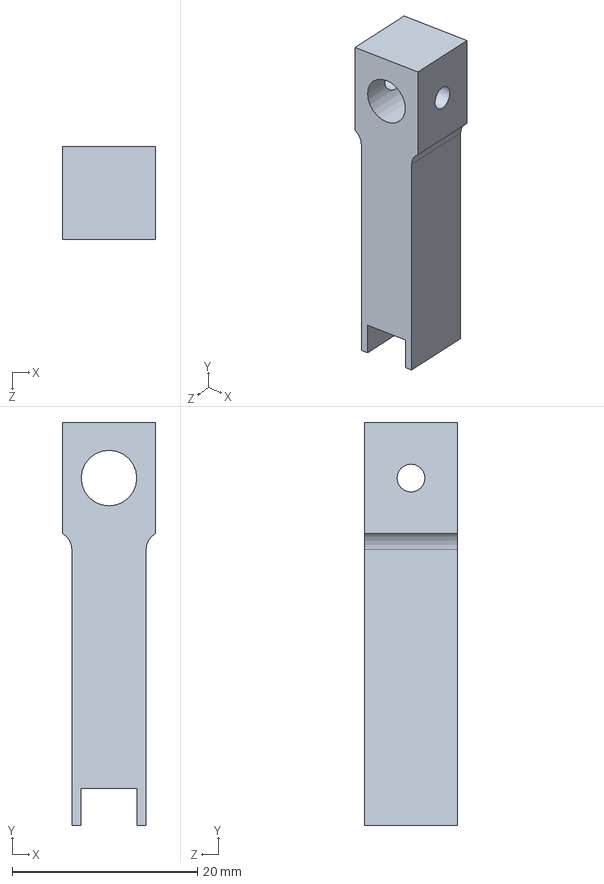
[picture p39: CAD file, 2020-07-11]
Mechanical Design/Holder/Moving Arm.SLDPRT
10.0 x 43.5 x 10.0 mm

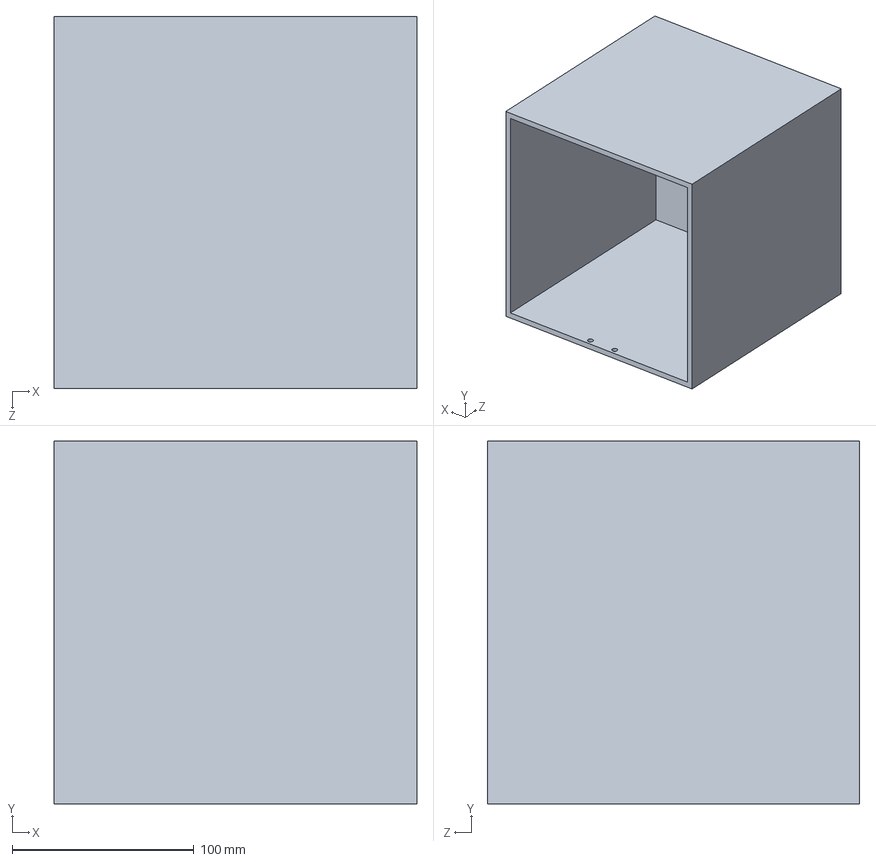
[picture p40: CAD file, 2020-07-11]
Mechanical Design/Pump/pump.SLDPRT
200.0 x 200.0 x 205.0 mm

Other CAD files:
Mechanical Design/Wiper/Right Wiper.SLDASM
Mechanical Design/Rinser/Ball bearing 8mm.SLDPRT
Mechanical Design/Vertical Assembly/Encoder.SLDPRT
Mechanical Design/Blower/120 mount.SLDPRT
Mechanical Design/Blower/blower2.SLDPRT
Mechanical Design/Extras/8mm slider.SLDPRT
Mechanical Design/Extras/Lead screw.SLDPRT
Mechanical Design/Holder/Base Arm.SLDPRT
Mechanical Design/Holder/Base Lock.SLDPRT
Mechanical Design/Holder/Lock Cover.SLDPRT
Mechanical Design/Holder/Rod.SLDPRT
Mechanical Design/Holder/Sliding key.SLDPRT
Mechanical Design/Holder/Temple support.sldprt
Mechanical Design/Inner box/8mm slider.SLDPRT
Mechanical Design/Inner box/Base.SLDPRT
Mechanical Design/Inner box/Cavity.SLDPRT
Mechanical Design/Inner box/Connector.SLDPRT
Mechanical Design/Inner box/Container.SLDPRT
Mechanical Design/Inner box/Glass.SLDPRT
Mechanical Design/Inner box/Lead screw VM.SLDPRT
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

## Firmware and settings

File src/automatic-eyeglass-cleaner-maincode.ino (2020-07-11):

#include <Wire.h>
#include <LiquidCrystal_I2C.h>
#include <Servo.h> 

/* PINS */

const int pump = 23; //relay_channel_1
const int blower = 52; //relay_channel_2
const int inValve = 24; //relay_channel_3
const int outValve = 25; //relay_channel_4
const int us_cleaner = 26; //relay_channel_5

const int main_ls_dir = 5; //cytron_motor_drive
const int main_ls_pwm = 6; //cytron_motor_drive
const int rnsr_ls_dir = 7; //cytron_motor_drive
const int rnsr_ls_pwm = 8; //cytron_motor_drive

const int wipr_dir = 9; //cytron_motor_drive
const int wipr_pwm = 10; //cytron_motor_drive

const int enc_A = 3; //encoder_pin_A
const int enc_B = 2; //encoder_pin_B

const int main_ls_hall = 11;

const int vsl_LOW = A0; //vessel_water_level_BOTTOM
const int vsl_HIGH = A1; //vessel_water_level_TOP
const int tank_LOW = A2; //tank_water_level_BOTTOM
const int tank_HIGH = A3; //tank_water_level_TOP

int servoPin = 4;

/* VARIABLES */

double z = 0.0; // vertical_coordinate
long counter = 0; // encoder revolution counter

  
/* VALUES */

const int main_ls_val = 50;
const int rnsr_ls_val = 100;
const int wipr_lft_val = 35;
const int wipr_rgt_val = 30;
const int cyt_stop_val = 0;
const int wipr_stop_val = 0;

const int vsl_lvl_ref = 1111;
const int tank_lvl_ref = 1111;

const int main_ls_up = HIGH;
const int main_ls_down = LOW;
const int rnsr_ls_left = HIGH;
const int rnsr_ls_right = LOW;
const int wipr_lft = HIGH;
const int wipr_rgt = LOW;

const int wipe_time = 2475;
const int rnsr_right_time = 3500;
const int rnsr_left_time = 3500;
const int wipr_lft_time = 550;
const int wipr_rgt_time = 550;
const int blow_time = 10000;

const int wipr_open_ang = 45;

const double ultrasonic = -45.0;
const double rinser = 15.0;
const double wiper = 23.0;

LiquidCrystal_I2C lcd = LiquidCrystal_I2C(0x27, 20, 4);
Servo Servo1;

void setup() {
  pinMode(pump,OUTPUT);
  pinMode(blower,OUTPUT);
  pinMode(inValve,OUTPUT);
  pinMode(outValve,OUTPUT);
  pinMode(us_cleaner,OUTPUT);
  pinMode(main_ls_dir,OUTPUT);
  pinMode(main_ls_pwm,OUTPUT);
  pinMode(rnsr_ls_dir,OUTPUT);
  pinMode(rnsr_ls_pwm,OUTPUT);
  pinMode(wipr_dir,OUTPUT);
  pinMode(wipr_pwm,OUTPUT);
  pinMode(enc_A,INPUT_PULLUP);
  pinMode(enc_B,INPUT_PULLUP);
  pinMode(vsl_LOW,INPUT);
  pinMode(vsl_HIGH,INPUT);
  pinMode(tank_LOW,INPUT);
  pinMode(tank_HIGH,INPUT);
  pinMode(main_ls_hall,INPUT);

  digitalWrite(pump,HIGH);
  digitalWrite(blower,HIGH);
  digitalWrite(inValve,HIGH);
  digitalWrite(outValve,HIGH);
  digitalWrite(us_cleaner,HIGH);

  attachInterrupt(digitalPinToInterrupt(enc_A),enc,CHANGE);

  Servo1.attach(servoPin);

  lcd.init();
  lcd.backlight();
  lcd.clear();
  lcd.setCursor(6,0);
  lcd.print("LensKart");
  lcd.setCursor(0,1);
  lcd.print("Open the front door and place the spectacle");
  Serial.begin(9600);
  //vertical(33.0,1);
}

void loop() {
    vertical(ultrasonic,-1);
    delay(70000);
    vertical(rinser,1);
    rinse();
    analogWrite(rnsr_ls_pwm,0);
    Servo1.write(0);
    delay(500);
    vertical(wiper,1);
    blow();
    wipe();
    vertical(0,-1);
    delay(60000);

}
void vertical(double m, double x) // m - target coordinate || x=1 for moving up || x=-1 for moving down
{
  if(x == 1)
  { 
    digitalWrite(main_ls_dir,main_ls_up);
    while(z <= m)
     {
      analogWrite(main_ls_pwm,main_ls_val);
      Serial.println(z);
     }
  }
  if(x == -1)
  { 
    digitalWrite(main_ls_dir,main_ls_down);
    while(z >= m)
    {
     analogWrite(main_ls_pwm,main_ls_val);
      Serial.println(z);
    } 
  }
  analogWrite(main_ls_pwm,cyt_stop_val);
}

void enc()
{
  if(digitalRead(enc_A) != digitalRead(enc_B))
   counter++;
  else
   counter--;
  z=counter/600;
}

int waterlvl(int x) //x=1 for vessel || x=2 for tank || returns 2-full 1-not_full 0-empty
{ 
  int a,b,c;
  if(x == 1)
  {
    a= vsl_LOW;
    b= vsl_HIGH;
    c= vsl_lvl_ref;
  }
  if(x == 2)
  {
    a= tank_LOW;
    b= tank_HIGH;
    c= tank_lvl_ref;
  }
  if(analogRead(a) > c)
   if(analogRead(b) > c)
    return 2;
   return 1;
  return 0;
}

void rinse()
{
 digitalWrite(rnsr_ls_dir,rnsr_ls_right);
 analogWrite(rnsr_ls_pwm,rnsr_ls_val);
 delay(rnsr_right_time);
 digitalWrite(rnsr_ls_dir,rnsr_ls_left);
 delay(rnsr_left_time);
 analogWrite(rnsr_ls_val,cyt_stop_val); 
}

void wipe()
{ 
  Servo1.write(wipr_open_ang);  
  delay(1000);
  long t = millis();
  while((millis()-t)<=wipe_time)
  {
  digitalWrite(wipr_dir,wipr_lft);
  analogWrite(wipr_pwm,wipr_lft_val);
  delay(wipr_lft_time);
  digitalWrite(wipr_dir,wipr_rgt);
  analogWrite(wipr_pwm,wipr_rgt_val);
  delay(wipr_rgt_time);
  }
  analogWrite(wipr_pwm,cyt_stop_val);
  Servo1.write(0);
  delay(1000);
}
void blow()
{
  digitalWrite(blower,LOW);
  delay(blow_time);
  digitalWrite(blower,HIGH);
}
void homestate()
{
  while(digitalRead(main_ls_hall)!=LOW)
  {
    digitalWrite(main_ls_dir,main_ls_down);
    analogWrite(main_ls_pwm,main_ls_val);
  }
  analogWrite(main_ls_pwm,cyt_stop_val);
}

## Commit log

2020-07-11 mechanical design.
    [8mm slider.SLDPRT, Ball bearing 8mm.SLDPRT, Base Arm.SLDPRT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]
2020-07-11 Pump Parts
    [box lid.SLDPRT, hinge1.SLDPRT, hinge2.SLDPRT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]
2020-07-11 Create Vertical Assembly
2020-07-11 Vertical Assembly Parts
    [Bevel gear.SLDPRT, Encoder Mount.sldprt, Encoder.SLDPRT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]
2020-07-11 Blower Parts
    [120 mount.SLDPRT, blower mount.SLDPRT, blower2.SLDPRT]
2020-07-12 Vertical Assembly snapshot-Updated
2020-07-12 Pump snapshot-Updated
